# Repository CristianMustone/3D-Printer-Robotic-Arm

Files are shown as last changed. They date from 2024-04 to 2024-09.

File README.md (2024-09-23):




# Robotic Arm 3D Printer #

A robotic arm with 3 degrees of freedom will be made, one prismatic and two rotating, with a SCARA – PRR type distribution.
The stepper motors corresponding to each degree of freedom will be controlled through an Arduino Uno together with L298N controllers.
A connection function via WIFI will be added with the integration of an ESP32 Cam, which communicates with the Arduino Uno, with which the G code file (.GCODE) of the part to be printed can be sent, and it will begin automatically . Communication between the computer where the G code is located and the ESP32 of the printer will be carried out through the website. With further development, it could be controlled over long distances through web pages, for example.
In a future application, the printing base could be replaced with a ribbon that withstands the extrusion temperature in order to have a level of serial production higher than most of the machines available on the market.

<table>
  <tr>
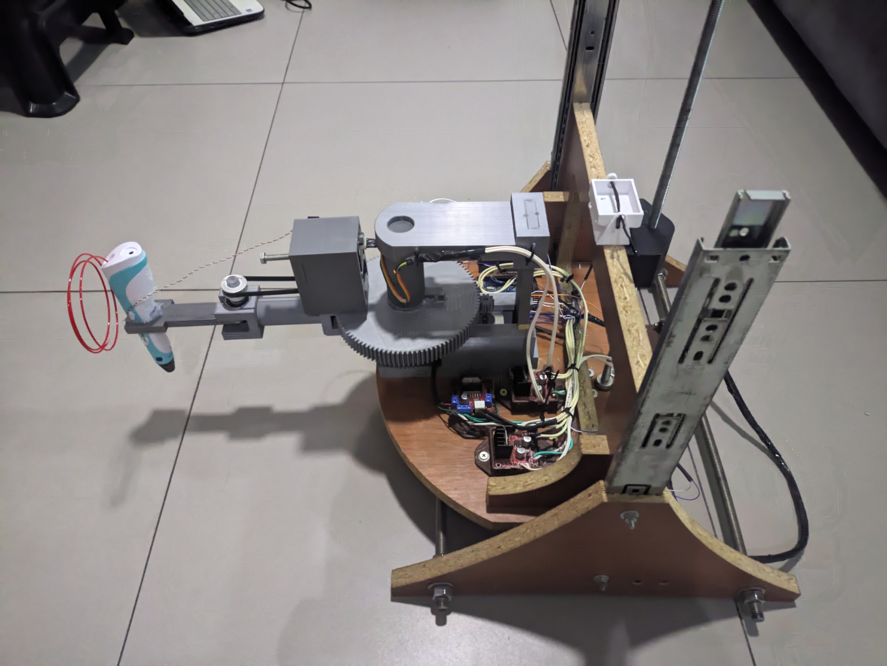
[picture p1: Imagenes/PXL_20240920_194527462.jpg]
Imagen 1
    <td></td>
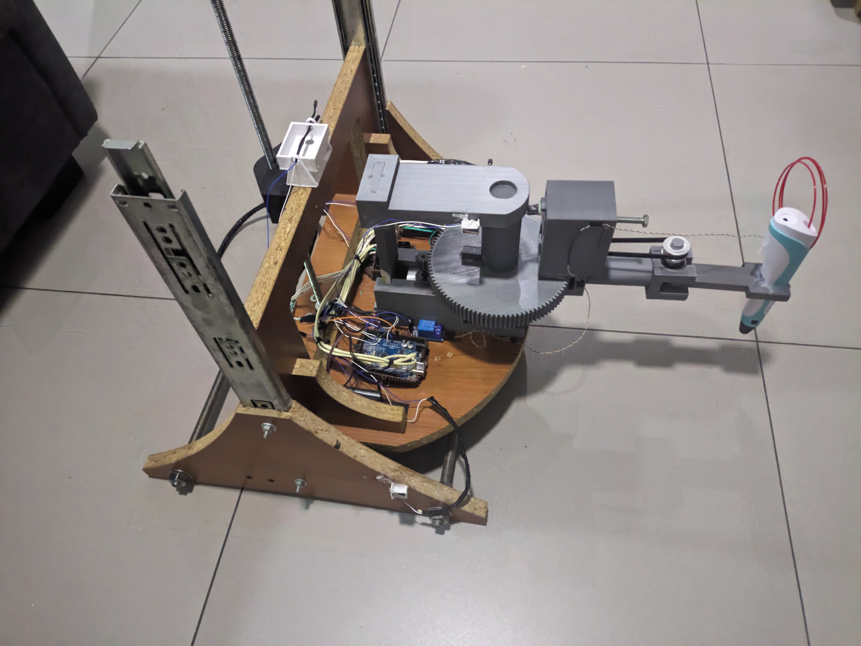
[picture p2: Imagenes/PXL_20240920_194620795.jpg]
Imagen 3
    <td></td>
  </tr>
  <tr>
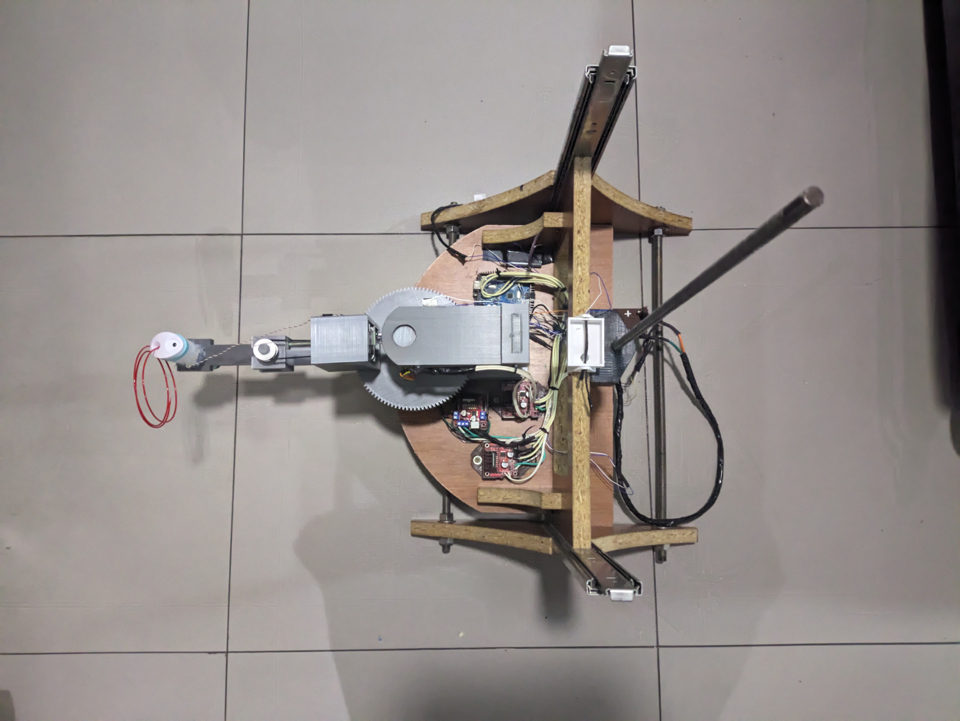
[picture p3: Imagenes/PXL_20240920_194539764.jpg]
Imagen 3
    <td></td>
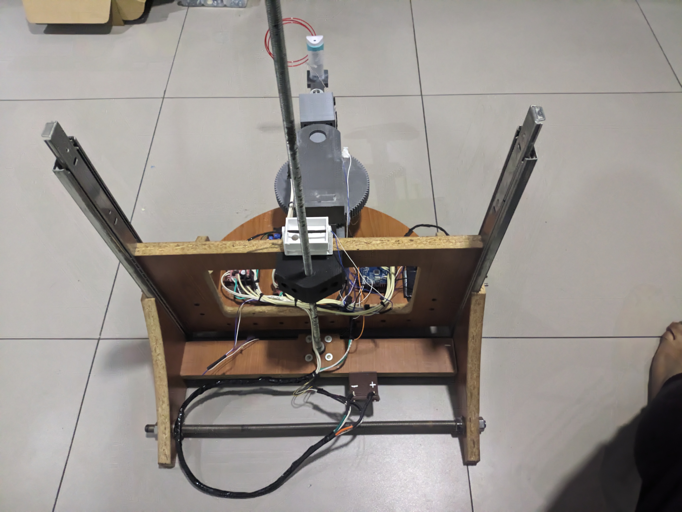
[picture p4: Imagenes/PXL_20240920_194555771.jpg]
Imagen 4
    <td></td>
  </tr>
  <tr>
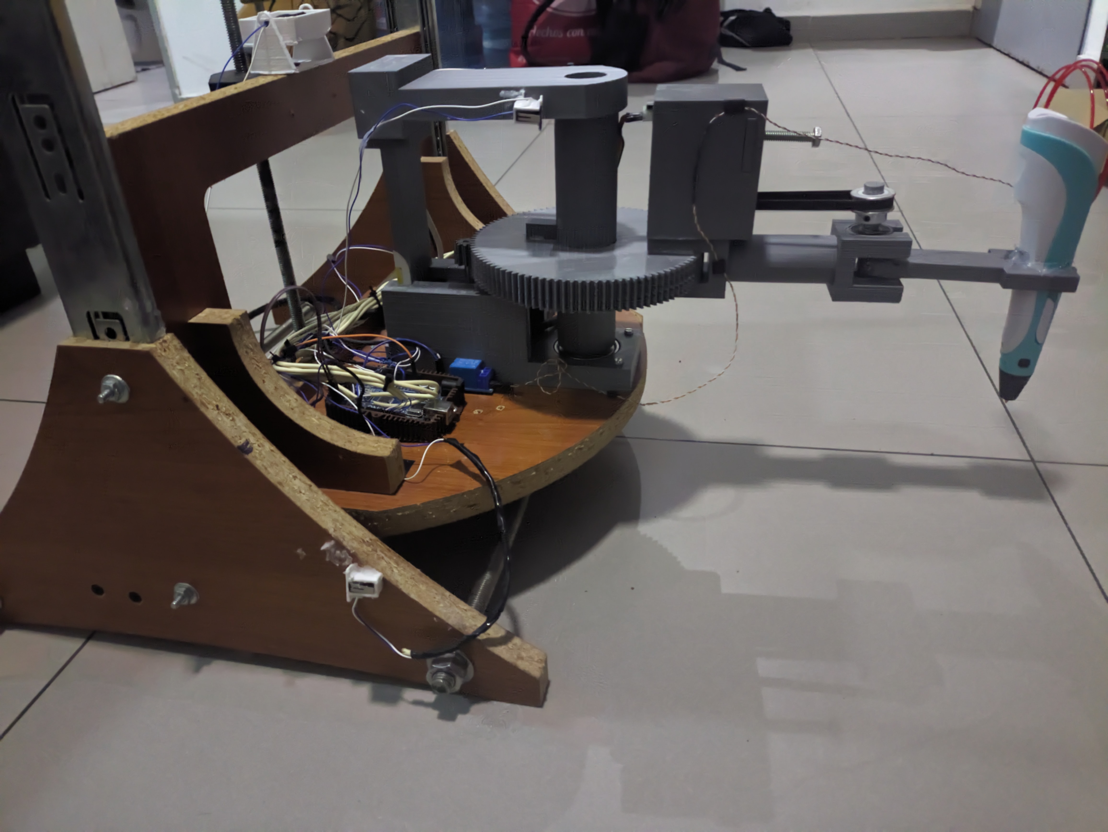
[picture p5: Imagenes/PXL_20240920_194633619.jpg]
Imagen 3
    <td></td>
    <td>Imagen 4</td>
  </tr>
</table>

## Goals

This project seeks to design a 3D printing system different from the most common models on the market, such as the 3-axis printer or those with an infinite axis. In addition, it will have greater printing capacity in terms of the size of the prints it can make, since being an instrument widely used today, there is a need to print larger pieces at once.
It also seeks to improve the human-printer relationship through online communication, either to show the progress of the printing or to attach a new job without having to connect it to a PC or through a compatible memory card.
Another objective is to be able to build a printer that entails lower manufacturing costs in order to compete with other printers on the market that have a higher price for equal or inferior features.

## Summary

A robotic arm with 3 degrees of freedom will be developed, with a configuration of 1 prismatic axis that will be used for the vertical movement of the extruder, and 2 rotary axes in SCARA format.
The advantage of this configuration is that it gives us a 180° printing area, a reach of 41 cm (base can be modified according to characteristics) and a height of approximately 30 cm. In total it would be a printing area of [Printing area calculation].
The parts to be used will be made of PLA, since they were designed and printed in 3D, wood, for the supports and components that require greater resistance, and finally the electronic components are integrated.
The operation is based on sending the file with a .gcode extension that is obtained from any laminator on the market (such as Cura) through a web page, and which can be printed automatically without requiring physical access to the machine. It will also have a camera that can be accessed from the same website to see the progress of the 3D printing made by the arm.

## Technical specifications

- The robotic arm must have an adequate range of motion to cover the minimum print area of 300x300x300.
- The robotic arm must be equipped with an extrusion tool that can print both PLA and ABS and the head itself must be able to be easily exchanged
- It must be operated through a Wi-Fi network from a web page with a user-friendly interface which is capable of loading a direct parameterized file to print and be able to initialize the operation as well as be able to see the process in real time through the application.
- The wireless connection must be stable and secure to guarantee fluid communication between the printer and the application.
- The structure of the robotic arm must be robust and resistant to ensure stable and safe operation.
- The manufacturing cost of the robotic arm should be as low as possible without compromising the quality and efficiency of the system.
- The robotic arm should be easy to disassemble and maintain to facilitate repair and replacement of parts in case of failure.Principle of form
- The structure must be stable and of simple design that guarantees possible future sizing applications.

# Materials

| Material | Quantity |
|---|:---:|
| L298N | x3 |
| Stepper NEMA 17 | x3|
| Cables |
| Arduino Uno | x1|
| ESP32 | x1|
| ESP32 CAM | x1|
| Wood |
| Power Supply 12v / 5v |
| Pencil 3D Printer | x1|
| Threaded Rod | x1|

## Selection criteria for each material

### ARDUINO UNO
The Arduino was selected as the motherboard for the movement of the motors due to the large number of libraries that can be found on the market for this type of boards, in addition to the ease they provide when programming the movement sequence.
The ESP32 or the ESP32 CAM was not used directly since, although the libraries can be adapted to this type of boards, the use of Wi-Fi required multiple use of pins to connect to the Internet and also move the motors, which generated unwanted signals that produced unwanted movements in the motors or their non-functioning at all.

### ESP32
This board was selected since it offers us the possibility of connecting to the Internet through an integrated Wi-Fi connection without the need to incorporate integrated devices.

### ESP32 CAM
This board was selected due to a similar criterion as the ESP32, it provides us with an integrated camera capable of transmitting video via Wi-Fi without a physical connection to the equipment through an IP address of the device.

## Design Specifications
It will be constructed constructively from parts made in 3D printing and wood, mainly ignoring the electronic and transmission components, the design will be based on figure 1 with modifications according to the needs.
The 3D printed parts were designed by ourselves. An approach was taken that with the smallest amount of material possible a part could be generated with the same functionality and that would withstand the conditions to which it was subjected. A 20% infill configuration was used and the material to be used was PLA.

# Software to Use

The following components will be programmed using C language:
ESP32: This will be used to communicate the webpage where the code is uploaded with the ARDUINO UNO.
ARDUINO UNO: This development board will be used to transform the code received from the user into one that the robot can use, and also to command the motors to be used.
ESP32 CAM: This will be used from the webpage for remote monitoring of the printing process.
A combination of HTML and CSS will also be used for the webpage design.

The steps for the complete functioning of the project are as follows:

1. File Upload: The file to be printed is uploaded to the webpage. This performs an HTTP POST of the file's content to a Google Sheets document. 
2. Handling from Google Sheets: The Google Sheets document is configured to, upon receiving an HTTP POST, capture all the sent content and place it line by line in the first column of its only sheet. Similarly, when it receives an HTTP GET, it sends all the information from the first column as a single string, where each line is separated by a comma.
3. Retrieval by the ESP32: The ESP32 is programmed to perform an HTTP GET to the Google Sheets document. Upon obtaining the string with the uploaded code, it executes a function to remove all unnecessary lines for motor operation, such as pre-configurations, extruder management, etc.
4. Sending to ARDUINO UNO: Once all the information is filtered, the ESP32 sends the newly generated string via the serial port (TX and RX) to the ARDUINO UNO.
5.The ARDUINO UNO performs further processing of the string where, for each command line of the code, it obtains the destination positions for both X and Y.
6. Once the positions are obtained, it calls a function that calculates the number of steps each motor needs to take according to our movement system.
7. With the number of steps calculated, we use another function that commands the motors to move the calculated number of steps, synchronously for the X and Y axes to maintain a stepped movement along the displacement vector.
8. Use of the ESP32 CAM: The ESP32 CAM code is set to work inversely to the ESP32. It generates an IP for the integrated camera and performs an HTTP POST with its IP address to another Google Sheets document.
9. When the webpage requests to view the printing progress, it first performs an HTTP GET to the Google Sheets document where the IP address of the ESP32 CAM is stored, then it directs to this address to display the video being recorded by the ESP32 CAM showing the printing progress.

## Explanation of how the code works
### Code explanation for the Arduino Uno
We are going to stop specifically at this point in order to detail the method of operation of the transformation of the Cartesian positions obtained to the number of steps that each motor must move along with the speed at which they must do so.
``` sh
while (Serial.available() > 0 && MensajeRecibido==0) {
    receivedMessage = Serial.readStringUntil('\r');
    Serial.println("Mensaje Recibido");
    Serial.println(receivedMessage);
    //miCadena.indexOf(subCadena)
    if ( receivedMessage.indexOf(",") != -1 && receivedMessage.indexOf(";") != -1){
      MensajeRecibido=1;
    }
```
This code fragment is used to enable reading the Serial port of the arduino while waiting for the message sent by the ESP32 with the string that has the lines of code to be executed by the robot.

``` sh
void MatrizMovimientos(char texto[]){
  for (int i = 0; i < strlen(texto); i++) {
    if (texto[i] == ';') {
      filas++;
    }
  }
  char *token = strtok(texto, ",;");
  for (int i = 0; i < filas; i++) {
    for (int j = 0; j < columnas; j++) {
      Movimientos[i][j] = atoi(token);
      // Serial.print("Valor Leido: ");
      // Serial.println(Movimientos[i][j]);
      token = strtok(NULL, ",;");
    }
  }
```
Next, the first function to use is to generate the Movement Matrix, that is, a list is created with the final positions of each axis for each line of code received. This generates a list with 3 values in each element, these values being the final positions of (X, Y, Z) .

``` sh
void moverRobotSCARA(float x, float y) {
  // Función para mover el robot SCARA a una posición específica
  int cuadrante = 0; 
  x=abs(x);
  y=abs(y);

  float d = sqrt(x * x + y * y);
  float phi = atan2(y, x);
  // Calcular los ángulos de las articulaciones mediante cinemática inversa
  float theta2 = acos((d * d - L1 * L1 - L2 * L2) / (2 * L1 * L2));
  float theta1 = phi - atan2(L2 * sin(theta2), L1 + L2 * cos(theta2));
  // Convertir los ángulos a pasos para los motores paso a paso
  float avanzar1 = ((theta1 - ultimo_step1) * 360)/(2 * PI);
  float avanzar2 = ((theta2 - ultimo_step2) * 360)/(2 * PI);

  int steps1 = avanzar1 / avance_motor;
  int steps2 = avanzar2 / avance_motor;

  MoverBrazo(steps1, steps2);

  ultimo_step1 = steps1;
  ultimo_step2 = steps2;
}
```

In the case of the moveRobotSCARA function, it is the one that transforms the final positions into the number of steps for each motor, only in the case of motors 1 and 2 (that is why it has 2 input values), representatives of the X and Y axes. , since, as they were defined as rotary type axes, a transformation from Cartesian coordinates to polar coordinates is necessary for their use.
Due to the configuration of the axes, it was decided to use the geometric method to calculate the angles to rotate in each motor in order to make the calculation simpler. We can observe the development of this method in the first lines of the function; converting them to mathematical language they would be:

$$ d = x2+ y2 $$

Calculates the distance from the origin to the end point where the extruder is located

$$phi = arc tangent (y,x)$$

To calculate the angle at which the end point is with respect to the horizontal axis

$$theta2 = arc cosine((d * d - L1 * L1 - L2 * L2) / (2 * L1 * L2))$$

L1 and L2 represent the lengths of arms 1 and 2 respectively.
This formula is used to calculate the angle between arm 2 and the continuation of the center line of arm 1.

$$theta1 = phi - arctangent(L2 * sine(theta2), L1 + L2 * cosine(theta2))$$

Finally, the angle of arm 1 with respect to the horizontal axis is calculated.

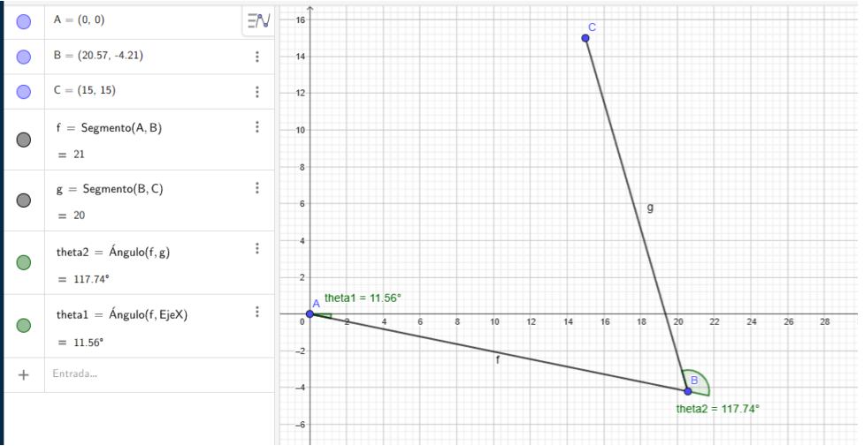
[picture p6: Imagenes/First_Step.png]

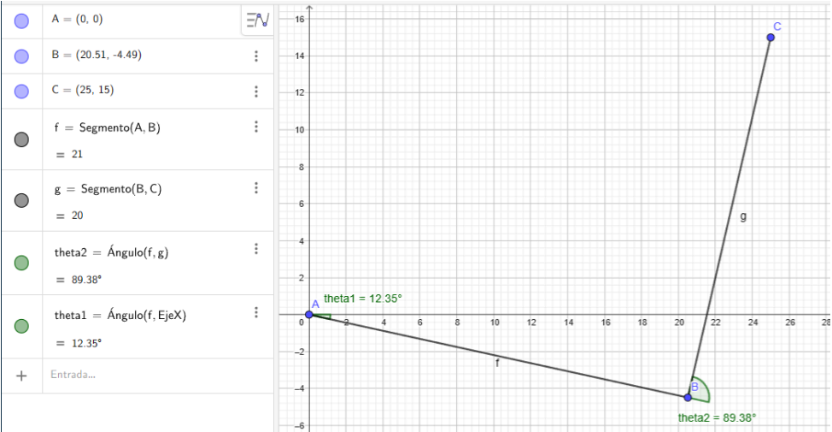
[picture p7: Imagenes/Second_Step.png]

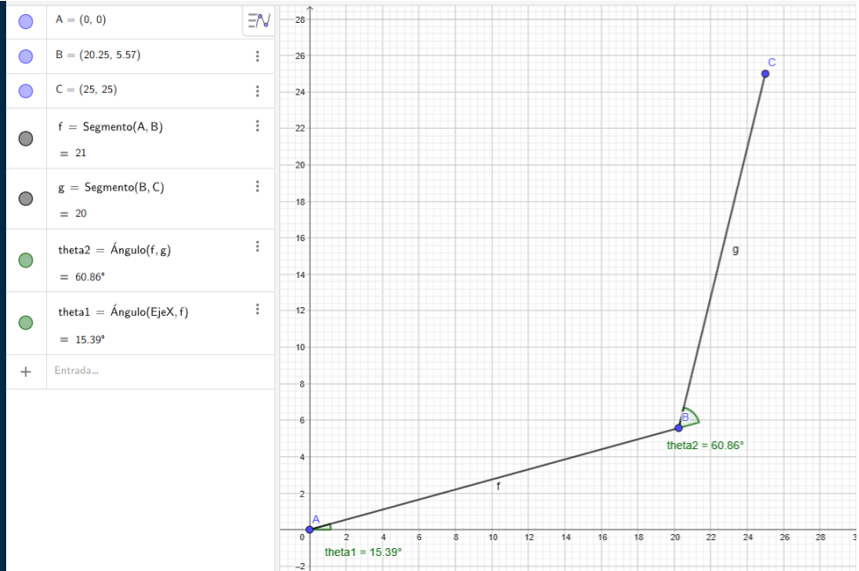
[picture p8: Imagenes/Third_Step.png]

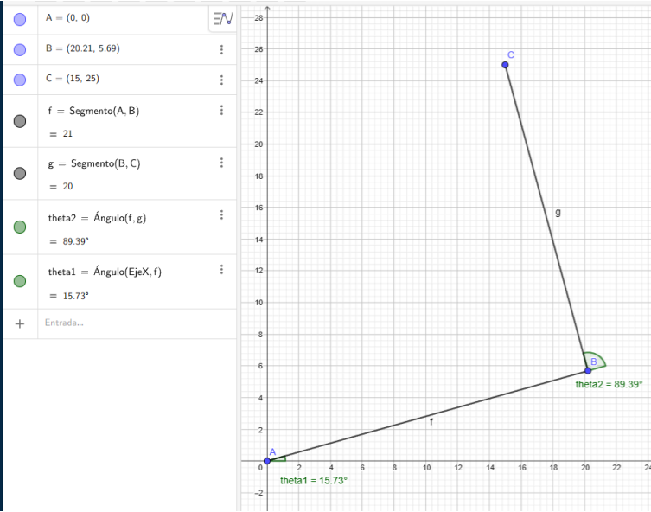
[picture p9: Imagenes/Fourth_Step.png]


Recreating the movement of the robot, the previous sequence of steps would look like:

video

With the sequence of end points (15,15); (25,15); (25,25); (15.25) the angles of theta1 and theta2 should be as follows:

```sh
  float avanzar1 = ((theta1 - ultimo_step1) * 360)/(2 * PI);
  float avanzar2 = ((theta2 - ultimo_step2) * 360)/(2 * PI);

  int steps1 = avanzar1 / avance_motor;
  int steps2 = avanzar2 / avance_moto
```
Next, the angles that each motor must advance (or retreat) are calculated. This is calculated by converting the calculated angles to geometric degrees, since they are initially found in non-representative values, that is, values that cannot be used as geometric degrees.
The angle at which the motor is currently located will also be subtracted, reflected in the variables ultimo_step1 and ultimo_step2, which, after each movement, will be updated. For example, if motor counterpart to advance1 but stops motor 2)
Finally, the number of degrees to move in each motor is divided by the degrees per step of the motor (in this case it would be 1.8 degrees per step, which is stored in the variable advance_motor), obtaining the number of steps to be performed to advance that number of geometric degrees.
```sh
MoverBrazo(steps1, steps2);
```
Once the entire series of calculations is finished, the MoveArm function is called, which is responsible for coordinating the movements of motors 1 and 2 so that they reach their destination at the same time, generating a straight line as a trajectory.
```sh
void MoverBrazo(int pasosX, int pasosY){
  int timeX = 0;
  int timeY = 0;
  int timetotal = 0;
  if (pasosX!=0 && pasosY!=0){
    float relacion = abs(pasosX)/abs(pasosY);
    stepDelayX = stepDelayX * pow(relacion,(-1));
  	timetotal = abs(pasosX) * stepDelayX;
  } else if (pasosY==0 && pasosX!=0){
  	timetotal = abs(pasosX)* stepDelayX;
  } else {
    timetotal = abs(pasosY)* stepDelayY;
  }

  for(int i=0;i<=timetotal;i++){
    if (i-timeX >= stepDelayX){
      if (pasosX>0){
        motorX.step(1);
      } else if (pasosX<0){
        motorX.step(-1);
      }
      timeX = i;
    }
    if (i-timeY >= stepDelayY){
      if (pasosY>0){
        motorY.step(1);
      } else if (pasosY<0){
          motorY.step(-1);
        }
      timeY = i;
  	}	
    delay(1);
  }
}
```
For motor hands to reach the destination point at the same time, regardless of the number of steps each one must take, there were several possibilities, such as using the Arduino milis library, but in this case it was decided to make a function with a Similar operation but with very short delay.
The operation of the MoverRoborSCARA function calculates the ratio of steps that motor 1 and 2 must take, once obtained, it affects the delay or internal speed of the motor with fewer steps by that factor, and it is obtained that both motors take the same even if they take a different number of steps. It should be noted that both motors already have a minimum speed for movement, so the factor is always additive.
Once the time that both motors will take to complete their corresponding steps has been calculated, a for loop is created that iterates for each millisecond of the total calculated, and at the end a delay of 1 millisecond is placed, this will cause each cycle of the loop to be executed every 1 millisecond. This allows us to see if the delay of each motor, that is, the number of milliseconds it takes to take each step, corresponds to the cycle number that is being executed, the motor moves one step. This affects both engines at the same time.
When you have to move a step regardless of the motor, a conditional is added to know if you have to move clockwise or counterclockwise, it could also be said, if you have to move one step or less one step.
As you can see, the operation of the Arduino milis library is very similar but with the addition of greater control over the total duration time.

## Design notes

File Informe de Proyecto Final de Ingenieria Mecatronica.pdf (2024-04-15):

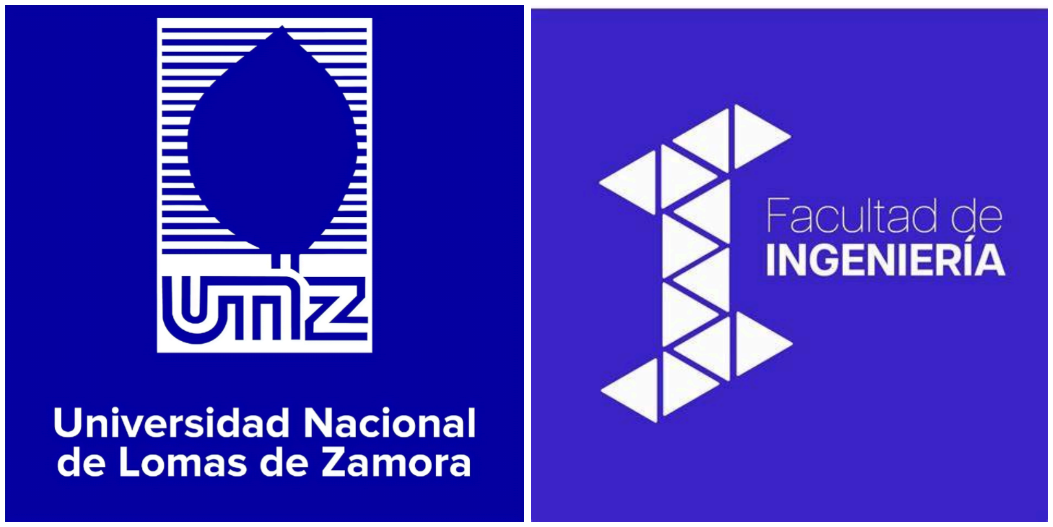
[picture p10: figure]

# INFORME

Alumnos:
Cristian Nahuel Castañares DNI: 42339695
MAIL: crismust99@gmail.com

Materia:
Proyecto Final de Ingeniería Mecatrónica

Carrera:
Ingeniería Mecatrónica

Facultad de Ingeniería - Universidad Nacional de Lomas de Zamora | 1

# Observaciones

Informe de proyecto final de Ingeniería Mecatrónica

Facultad de Ingeniería - Universidad Nacional de Lomas de Zamora | 2

# Armado de brazo robótico para imprimir en3D utilizando plástico fundido

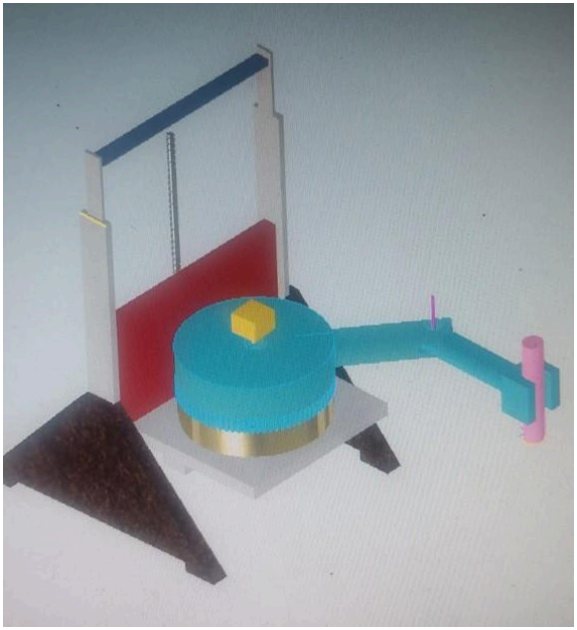
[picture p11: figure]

Facultad de Ingeniería - Universidad Nacional de Lomas de Zamora | 3

# Índice

Facultad de Ingeniería - Universidad Nacional de Lomas de Zamora | 4

# 1.Presentación

## 1.1 Introducción

Se realizará un brazo robótico de 3 grados de libertad, uno prismático y dos rotativos, con una distribución tipo SCARA – PRR.
Se controlarán los motores paso a paso correspondientes a cada grado de libertad, a través de un Arduino Uno junto con controladores Pololu A4988.
Se agregará una función de conexión a través de WIFI con la integración de un ESP32 Cam, que se intercomunica con el Arduino Uno, con el cual se podrá enviar el archivo en código G (.GCODE) de la pieza a imprimir, y comenzará automáticamente. La comunicación entre la computadora donde se encuentra el código G y el ESP32 de la impresora, se realizará a través de la pagina web. Con un desarrollo mayor, se podría controlar a distancias grandes a través de páginas web, por ejemplo.
En una futura aplicación se podría reemplazar la base de impresión por una cinta que soporte la temperatura de extrusión a fin de poder contar con un nivel de producción en serie superior a la mayoría de las máquinas disponibles en el mercado.

Facultad de Ingeniería - Universidad Nacional de Lomas de Zamora | 5

## 1.2 Objetivos

- En este proyecto se busca diseñar un sistema de impresión 3D diferente a los modelos más comunes del mercado, como la impresora de 3 ejes o las de un eje infinito. Además, tendrá mayor capacidad de impresión en cuanto al tamaño de las impresiones que pueda realizar, ya que al ser un instrumento bastante utilizado en la actualidad, nace una necesidad de imprimir piezas más grandes de una sola vez.
- También se busca mejorar la relación humano – impresora a través de una comunicación online, ya sea para mostrar el avance de la impresión como también adjuntarle un nuevo trabajo sin necesidad de conectarla a una PC o a través de una tarjeta de memoria compatible.
- Otro de los objetivos es poder construir una impresora que conlleve un menor gasto de fabricación para así competir con demás impresoras en el mercado que posean un precio mayor por características iguales o inferiores.

Facultad de Ingeniería - Universidad Nacional de Lomas de Zamora | 6

## 1.3 Alcance

- Para el alcance de este proyecto, se tendrán en cuentas las siguientes modificaciones al proyecto inicialmente descripto:
- Se reemplazará el extrusor normalmente utilizado en impresoras 3D por un lápiz que cumple la misma funcionalidad pero con la ventaja de ser mucho más sencillo de utilizar.
- No se tendrá en cuenta el eje infinito para producción en serie, y se trabajará solamente con el área de impresión física del robot.
- La comunicación entre la computadora y la impresora será a través de wifi en la cual ambos dispositivos deberán estar conectado a la misma red.

Facultad de Ingeniería - Universidad Nacional de Lomas de Zamora | 7

## 1.4 Resumen

Se elaborará un brazo robótico de 3 grados de libertad, con una configuración de 1 eje prismático que se utilizara para el movimiento vertical de la extrusora, y 2 ejes rotativos en formato SCARA.
La ventaja de esta configuración es que nos da un área de impresión de 180°, un alcance de 41 cm (de base pudiendo modificar según características) y una altura de 30 cm aproximadamente. En total seria una area de impresion de [Calculo del area de impresion]. Las piezas a utilizar serán de PLA, ya que se diseñaron e imprimieron en 3D, madera, para los soportes y componentes que requieran una resistencia mayor, y por último se integran los componentes electrónicos.
El funcionamiento se basa en el envío del archivo con extensión .gcode que se obtiene en cualquier laminador del mercado (como por ejemplo Cura) a través de una página web, y que pueda imprimirse automáticamente sin necesitar de tener acceso físico a la máquina. También contará con una cámara a la que se podrá acceder desde la misma página web para ir viendo el avance de la impresión 3D realizada por el brazo.

Facultad de Ingeniería - Universidad Nacional de Lomas de Zamora | 8

# 2. Ingeniería de la solución

## 2.1 Especificaciones técnicas:

- El brazo robótico debe tener un rango de movimiento adecuado para cubrir el área de impresión mínima de 300x300x300.
- El brazo robótico debe estar equipado con una herramienta de extrusión que pueda imprimir tanto pla como abs y el mismo cabezal debe ser capaz de intercambiarse fácilmente
- Se debe operar mediante una red wifi a partir de una página web con una interfaz amigable con el usuario la cual sea capaz de cargar un archivo parametrizado directo para imprimir y poder inicializar la operación así como poder ver mediante el aplicativo el proceso en tiempo real
- La conexión inalámbrica debe ser estable y segura para garantizar una comunicación fluida entre la impresora y el aplicativo.
- La estructura del brazo robótico debe ser robusta y resistente para garantizar una operación estable y segura.
- El costo de fabricación del brazo robótico debe ser lo más bajo posible sin comprometer la calidad y la eficiencia del sistema.
- El brazo robótico debe ser fácil de desmontar y mantener para facilitar la reparación y el reemplazo de piezas en caso de fallos.Principio del formulario
- La estructura debe ser estable y de diseño simple que garantice posibles aplicaciones de dimensionamiento a futuro.

## 2.2 Detalle de pines a utilizar

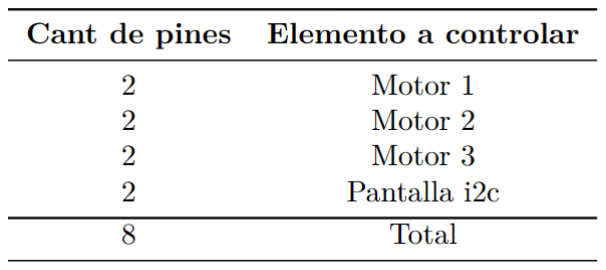
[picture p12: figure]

Facultad de Ingeniería - Universidad Nacional de Lomas de Zamora | 9

## 2.3 Materiales a utilizar

### 2.3.1 Presupuesto

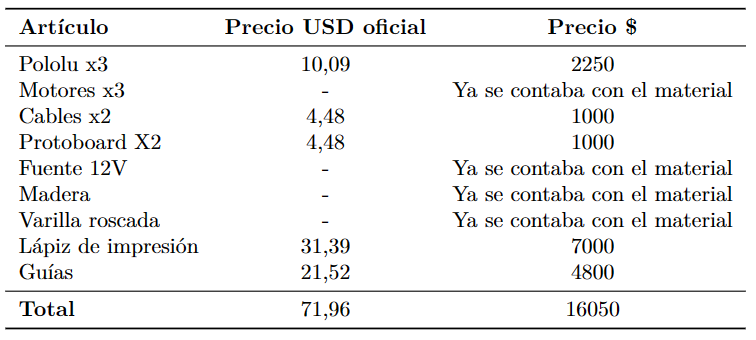
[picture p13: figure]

### 2.3.2 Criterio de selección de cada material

ARDUINO UNO
Se seleccionó el Arduino como placa base para el movimiento de los motores debido a la gran cantidad de librerías que se pueden encontrar en el mercado para este tipo de placas, además de la facilidad que otorgan a la hora de programar la secuencia de movimiento.
No se utilizó directamente el ESP32 o el ESP32 CAM ya que, si bien puede adaptarse las librerías a este tipo de placas, el uso del wifi requería multiuso de pines para conectarse a internet y además mover los motores, lo cual generaba señales indeseadas que producían movimientos no deseados en los motores o directamente su no funcionamiento.

ESP32
Se seleccionó esta placa ya que nos ofrece la posibilidad de conectarnos a internet a través de una conexión wifi integrada sin necesidad de incorporar integrados.

ESP32 CAM
Esta placa se seleccionó debido a un criterio similar al del ESP32, nos brinda una cámara integrada capaz de transmitir video a través de wifi sin conexión física con el equipo a través de una dirección IP del dispositivo.

## 2.4 Especificaciones de Diseño

El mismo será construido constructivamente a partir de piezas elaboradas en impresión 3D y madera principalmente obviando los componentes electrónicos y de transmisión, el diseño será basado en la figura 1 con las modificaciones acordes a las necesidades.
Las piezas impresas en 3D fueron diseñadas por nosotros mismos. Se tuvo un enfoque de que con la menor cantidad de material posible se pueda generar una pieza con la misma

Facultad de Ingeniería - Universidad Nacional de Lomas de Zamora | 10

funcionalidad y que soportara las condiciones a la que se estaba sometido. Se utilizó una configuración de relleno del 20% y el material a utilizar fue PLA.
Para las piezas compuestas por madera, se utilizó una cortadora láser y tablas de [material].

[piezas impresas]

## 2.5 Software a utilizar

Se usará lenguaje C para programar los siguientes componentes:
- ESP32: El cual se utilizará para comunicar la página web donde se depositara el código con el ARDUINO UNO.
- ARDUINO UNO: Se utilizará esta placa de desarrollo para la transformación del código recibido por el usuario a uno que el robot pueda utilizar, y además para el comando de los motores a utilizar.
- ESP32 CAM: En este caso se utilizará desde la página web para el seguimiento de la impresión a distancia.
También se utilizará una combinación de HTML y CSS para el diseño de la página web.

Los pasos a seguir para el funcionamiento completo del proyecto son:

### 1. Subida del archivo: Se sube el archivo que se quiere imprimir a la página web. Esta

realiza un HTTP POST del contenido del archivo a un archivo de Google sheets

### 2. Manejo desde Google Sheets: El archivo de Google Sheets está configurado para

que cuando recibe un HTTP POST, obtenga todo el contenido que se le ha enviado y lo coloque por línea en la primera columna de la única hoja que se encuentra en el documento. De la misma forma, cuando recibe un HTTP GET, envía toda la información de la primera columna en un solo string, en el cual cada línea está separada por una coma.

### 3. Obtención desde el ESP32: El ESP32 está programado para realizar un HTTP

GET al archivo del Google Sheets. Cuando obtiene el string con el código subido, ejecuta una función que elimina todas las líneas innecesarias para el funcionamiento de los motores, ya sean pre configuraciones, manejo del extrusor, etc.

### 4. Envío al ARDUINO UNO: Una vez filtrada toda la información, el ESP32 envía el

nuevo string generado a través del puerto serie (TX y RX) hacia el ARDUINO UNO.
a. Este hace un segundo manejo del string en donde, por cada línea de comando del código, obtiene las posiciones de destino tanto de X como Y.
b. Una vez obtenidas las posiciones, manda a llamar a la función que calcula la cantidad de pasos que debe realizar cada motor según nuestro sistema de movimiento.
c. Cuando calcula la cantidad de pasos manda a llamar a otra función que es la que comanda a los motores, diciendo que se muevan la cantidad de pasos calculados, junto con una configuración para manejar los tiempos de movimiento de cada motor.

### 5. Uso del ES32 CAM: El código del ESP32 CAM está seteado para funcionar a la

inversa del ESP32, este genera una IP para la cámara que está integrada, y realiza un HTTP POST con su dirección IP a otro archivo de Google Sheets.
Cuando la página web solicita ver el avance de la impresión, realiza primero un HTTP GET al archivo de Google Sheets donde esta la direccion IP de la cámara del

Facultad de Ingeniería - Universidad Nacional de Lomas de Zamora | 11

ESP32 CAM, para dirigirse a esta y mostrar el video que está filmando el ESP32 CAM con el avance de la impresión.

### 2.5.1 Código del ESP32

Para este caso, a fin de un mejor control, orden y revisión del código, se decidió separarlo en 2 módulos complementarios. En uno se definen las funciones que se van a utilizar mientras en el otro se utilizan y arma el código general.
El módulo general quedaría de la siguiente forma:

#include <HardwareSerial.h>

#include <WiFi.h>

#include <HTTPClient.h>

#include <string.h>

#define esp32TX 1 // Puedes ajustar los pines según tu configuración #define esp32RX 3

#define WIFI_SSID "PCwifi"

#define WIFI_PASSWORD "ingmustone"

String GOOGLE_SCRIPT_ID =
"AKfycbxiWrbWpRyaDDQQgARydaQq3UQNIaPEfO08l73xLwA0IrmX1_svnYCXUWWWk37 KXSlUqg";

#define MAX_COMMAND_LENGTH 255

int SendMessage=0;
char gcode_string[1024]; // Tamaño suficiente para almacenar las líneas del archivo int FileOk = 1;
const char* payloadCopy;
int Filas = 0;
int Movimientos[50][3]; // cantidad de filas que va contener se estima en 50 por ahora char Mensaje[1024]="";

void setup() {
Serial.begin(115200);
Serial2.begin(2400, SERIAL_8N1, esp32RX, esp32TX); // Inicializa Serial2 con pines personalizados

String payload;

WiFi.begin(WIFI_SSID, WIFI_PASSWORD);

while (WiFi.status() != WL_CONNECTED) { delay(500);

Facultad de Ingeniería - Universidad Nacional de Lomas de Zamora | 12

Serial.println("Conectando");
}

HTTPClient http;
String url="https://script.google.com/macros/s/"+GOOGLE_SCRIPT_ID+"/exec?read"; http.begin(url.c_str()); //Specify the URL and certificate http.setFollowRedirects(HTTPC_STRICT_FOLLOW_REDIRECTS);
int httpCode = http.GET();
if (httpCode > 0) { //Check for the returning code
payload = http.getString();
payloadCopy=payload.c_str(); Serial.println("HTTP ok");
}
http.end();

}

void loop() {
if (SendMessage==0){
strcpy(gcode_string, payloadCopy); Serial.println("Armando Matriz de Movimientos"); MatrizDeMovimientos(gcode_string); Serial.println("Matriz Armada");

for (int Fila=0; Fila<Filas; Fila++){
char numero[20];
sprintf(numero, "%d", Movimientos[Fila][0]); strcat(Mensaje, numero);
strcat(Mensaje,",");
sprintf(numero, "%d", Movimientos[Fila][1]); strcat(Mensaje, numero);
strcat(Mensaje,",");
sprintf(numero, "%d", Movimientos[Fila][2]); strcat(Mensaje, numero);
strcat(Mensaje,";");
}

Serial2.println(Mensaje);
SendMessage=1;
}
}

Mientras que el módulo de las funciones quedaría de la siguiente forma:

bool TryCatch (char Letra, const char* line){
char* Pos=0;
//PosZ=*(strchr(line,'Z'));

Facultad de Ingeniería - Universidad Nacional de Lomas de Zamora | 13

bool success = true;
Pos=strchr(line,Letra);
return success;
}

void extractSubstring(const char* input, char* output, size_t startIndex, size_t length) { size_t inputLength = strlen(input);
if (startIndex >= inputLength) {
// Error: startIndex está fuera de los límites de la cadena de entrada
return;
}
size_t endIndex = startIndex + length;
if (endIndex > inputLength) {
// Ajustar endIndex si excede la longitud de la cadena de entrada endIndex = inputLength;
}

strncpy(output, input + startIndex, endIndex - startIndex); output[endIndex - startIndex] = '\0';
}

void MatrizDeMovimientos(char* gcode_string){
int comandoG = 0;
char* line;
line = strtok(gcode_string, ",");
while (line != NULL) {
if (line[0] == 'G') {
comandoG = 1;

char newX[20]="0";
char newY[20]="0";
char newZ[20]="0";
char* PosX = 0;
char* PosY = 0;
char* PosZ = 0;
char* PosE = 0;
bool Fx, Fy, Fz, Fe = true; size_t Px,Py,Pe,Pz=0;

switch (line[1]){
case '0':
/*X e Y Siempre
E nunca
Z quizas*/
//------------------------------------- Extrayendo Z si la hay ----------------------------if (TryCatch('Z',line)){
PosZ=strchr(line,'Z');
Pz = PosZ - line;

Facultad de Ingeniería - Universidad Nacional de Lomas de Zamora | 14

size_t lengthZ = strlen(line) - Pz;
extractSubstring(line, newZ, Pz + 1, lengthZ);
Fz = true;
} else {
Fz = false;
}
//------------------------------------- Extrayendo X e Y ----------------------------//obtengo la posicion de X e Y

PosX=strchr(line,'X');
Px= PosX - line;
Fx = true;

PosY=strchr(line,'Y');
Py = PosY - line;
Fy = true;

if (Fx && Fy){
size_t lengthX = Py - Px - 1; extractSubstring(line, newX, Px + 1, lengthX); }
if (Fy && Fz){
size_t lengthY = Pz - Py - 1; extractSubstring(line, newY, Py + 1, lengthY); } else {
size_t lengthY = strlen(line) - Py + 1; extractSubstring(line, newY, Py + 1, lengthY); }

Movimientos[Filas][0] = atof(newX); Movimientos[Filas][1] = atof(newY); Movimientos[Filas][2] = atof(newZ);

break;

case '1':
/*X e Y quizas
E siempre
Z nunca*/
//------------------- Revisando si hay X e Y ---------------------------------if (TryCatch('X',line)){
PosX=strchr(line,'X');
Px= PosX - line;
Fx=true;
} else {
Fx = false;
}

Facultad de Ingeniería - Universidad Nacional de Lomas de Zamora | 15

if (TryCatch('Y',line)){
PosY=strchr(line,'Y');
Py = PosY - line;
Fy=true;
} else {
Fy = false;
}
if (TryCatch('E',line)){
PosE=strchr(line,'E');
Pe = PosE - line;
Fe=true;
} else {
Fe = false;
}
if (Fx && Fy){
size_t lengthX = Py - Px - 1; extractSubstring(line, newX, Px + 1, lengthX); }
if (Fy && Fe){
size_t lengthY = Pe - Py - 1; extractSubstring(line, newY, Py + 1, lengthY); }

Movimientos[Filas][0] = atof(newX); Movimientos[Filas][1] = atof(newY); Movimientos[Filas][2] = 0;

break;
default:
break;
}
Filas++;
}
line = strtok(NULL, ",");
}
}

### 2.5.2 Código para el Arduino Uno

En este caso también se decidió tener dos módulos similares al caso anterior. De los cuales el código general quedaría:

#include <Stepper.h>

#include <math.h>

#include <stdlib.h>

#include <string.h>

Facultad de Ingeniería - Universidad Nacional de Lomas de Zamora | 16

String receivedMessage = "";
int MensajeRecibido = 1;

// Define el número de pasos por vuelta del motor
const int stepsPerRevolutionZ = 200; //suponiendo que es 1mm por vuelta const int stepsPerRevolutionX = 1600; //suponiendo que la relacion es 80:1 const int stepsPerRevolutionY = 200; //la relacion es 1:1

// Define los pines de control para el driver L298N
const int motor1Pins[] = {2,3, 4, 5}; // IN1, IN2, IN3, IN4
const int motor2Pins[] = {6, 7, 8, 9}; // IN1, IN2, IN3, IN4
const int motor3Pins[] = {10, 11, 12, 13}; // IN1, IN2, IN3, IN4

int filas = 0, columnas = 3;
int Movimientos[50][3]; // cantidad de filas que va contener se estima en 50 por ahora

#define L1 21.0 // Longitud del primer eslabón en unidades de longitud

#define L2 20.0 // Longitud del segundo eslabón en unidades de longitud

#define avance_motor 1.8

// Crea objetos Stepper para cada motor
Stepper motorX(stepsPerRevolutionX, motor1Pins[0], motor1Pins[1], motor1Pins[2], motor1Pins[3]);
Stepper motorY(stepsPerRevolutionY, motor2Pins[0], motor2Pins[1], motor2Pins[2], motor2Pins[3]);
Stepper motorZ(stepsPerRevolutionZ, motor3Pins[0], motor3Pins[1], motor3Pins[2], motor3Pins[3]);

int stepDelayX = 25;
int stepDelayY = 25;

float ultimo_step1 = 0;
float ultimo_step2 = 0;
float ultimo_step3 = 0;

void setup() {
// Establece la velocidad de los motores
motorX.setSpeed(stepDelayX); // Puedes ajustar esta velocidad según sea necesario motorY.setSpeed(stepDelayY);
motorZ.setSpeed(20);
}

void loop() {

//receivedMessage="G0 F600 X15 Y15 Z10,G1 X25 Y15 E0.94529,G1 X25 Y25 E0.94529,G1 X15 Y25 E0.94529";

Facultad de Ingeniería - Universidad Nacional de Lomas de Zamora | 17

while (Serial.available() > 0 && MensajeRecibido==0) {
receivedMessage = Serial.readStringUntil('\r'); Serial.println("Mensaje Recibido");
Serial.println(receivedMessage);
//miCadena.indexOf(subCadena)
if ( receivedMessage.indexOf(",") != -1 && receivedMessage.indexOf(";") != -1){ MensajeRecibido=1;
}
}

if (MensajeRecibido==1){
const char* charMessage = receivedMessage.c_str(); MatrizMovimientos(charMessage);
for (int fila=0; fila <filas; fila++){ motorZ.step(Movimientos[fila][2]*stepsPerRevolutionZ - ultimo_step3); moverRobotSCARA(Movimientos[fila][0], Movimientos[fila][1]); ultimo_step3 = Movimientos[fila][2]*stepsPerRevolutionZ;
}
Serial.println("Terminado");
MensajeRecibido = 0;
receivedMessage = ""; // Limpiar el mensaje recibido delay(1000);
}
for (int i = 0; i < filas; i++) {
for (int j = 0; j < columnas; j++) { Movimientos[i][j] = 0;
}
}
filas=0;
}

Mientras que el módulo de funciones quedaría de la siguiente forma:

void MatrizMovimientos(char texto[]){
for (int i = 0; i < strlen(texto); i++) {
if (texto[i] == ';') {
filas++;
}
}
char *token = strtok(texto, ",;"); for (int i = 0; i < filas; i++) {
for (int j = 0; j < columnas; j++) { Movimientos[i][j] = atoi(token); // Serial.print("Valor Leido: ");
// Serial.println(Movimientos[i][j]); token = strtok(NULL, ",;");
}

Facultad de Ingeniería - Universidad Nacional de Lomas de Zamora | 18

}
}

void moverRobotSCARA(float x, float y) {
// Función para mover el robot SCARA a una posición específica int cuadrante = 0;
x=abs(x);
y=abs(y);

float d = sqrt(x * x + y * y);
float phi = atan2(y, x);
// Calcular los ángulos de las articulaciones mediante cinemática inversa float theta2 = acos((d * d - L1 * L1 - L2 * L2) / (2 * L1 * L2));
float theta1 = phi - atan2(L2 * sin(theta2), L1 + L2 * cos(theta2));
// Convertir los ángulos a pasos para los motores paso a paso
float avanzar1 = ((theta1 - ultimo_step1) * 360)/(2 * PI);
float avanzar2 = ((theta2 - ultimo_step2) * 360)/(2 * PI);

int steps1 = avanzar1 / avance_motor;
int steps2 = avanzar2 / avance_motor;

MoverBrazo(steps1, steps2);

ultimo_step1 = steps1;
ultimo_step2 = steps2;
}

void MoverBrazo(int pasosX, int pasosY){ int timeX = 0;
int timeY = 0;
int timetotal = 0;
if (pasosX!=0 && pasosY!=0){
float relacion = abs(pasosX)/abs(pasosY); stepDelayX = stepDelayX * pow(relacion,(-1)); timetotal = abs(pasosX) * stepDelayX;
} else if (pasosY==0 && pasosX!=0){ timetotal = abs(pasosX)* stepDelayX;
} else {
timetotal = abs(pasosY)* stepDelayY;
}

for(int i=0;i<=timetotal;i++){
if (i-timeX >= stepDelayX){
if (pasosX>0){
motorX.step(1);
} else if (pasosX<0){
motorX.step(-1);
}

Facultad de Ingeniería - Universidad Nacional de Lomas de Zamora | 19

timeX = i;
}
if (i-timeY >= stepDelayY){ if (pasosY>0){
motorY.step(1);
} else if (pasosY<0){
motorY.step(-1);
}
timeY = i;
}
delay(1);
}
}

### 2.5.3 Código para el ESP32 CAM

#include <WiFi.h>

#include <HTTPClient.h>

const char* ssid = "Repetidor";
const char* password = "53EW9e527c2fAeBb3a2d";
const char* spreadsheetId = "13_MIWFoQno4I7jppms3PyK7UoSv1RYUoeWZiwnOPLt0"; const char* sheetName = "Hoja 1";
const char* apiKey = "0e1c00f2a8ca7bc3949755c1b3a4f3386d19e63f";

void setup() {
Serial.begin(115200);
delay(2000);

WiFi.begin(ssid, password);
while (WiFi.status() != WL_CONNECTED) { delay(1000);
Serial.println("Conectando a WiFi...");
}

Serial.println("Conectado a WiFi");

sendDataToGoogleSheets("Hola mundo");
}

void loop() {
// No se requiere ninguna acción en el bucle principal }

void sendDataToGoogleSheets(const String& data) { HTTPClient http;

// Construir la URL de solicitud

Facultad de Ingeniería - Universidad Nacional de Lomas de Zamora | 20

String url = "https://sheets.googleapis.com/v4/spreadsheets/";
url += spreadsheetId;
url += "/values/";
url += sheetName;
url += ":append?valueInputOption=USER_ENTERED&key="; url += apiKey;

// Configurar la solicitud HTTP
http.begin(url);
http.addHeader("Content-Type", "application/json");

// Construir el cuerpo de la solicitud
String jsonBody = "{\"values\": [[\"";
jsonBody += data;
jsonBody += "\"]]}";

// Enviar la solicitud HTTP POST
int httpResponseCode = http.POST(jsonBody);

if (httpResponseCode > 0) {
Serial.print("Datos enviados a Google Sheets. Código de respuesta: "); Serial.println(httpResponseCode);
} else {
Serial.print("Error en la solicitud. Código de error: "); Serial.println(httpResponseCode);
}

http.end();
}

### 2.5.4 Código para la página web

<!DOCTYPE html>
<html>
<head>
<title>Subir archivo de texto y enviar contenido</title>

<script>
function mostrarContenido() {
var fileInput = document.getElementById('archivo'); var file = fileInput.files[0];
var reader = new FileReader();

reader.onload = function(e) {
var contenido = e.target.result;
sessionStorage.setItem('contenidoArchivo', contenido); enviarContenido(contenido); // Llamar a la función para enviar el contenido };

Facultad de Ingeniería - Universidad Nacional de Lomas de Zamora | 21

reader.readAsText(file);
}

function enviarContenido(contenido) {
var messageElement = document.createElement('p'); // Crear un elemento <p> para mostrar el mensaje
document.body.appendChild(messageElement); // Agregar el elemento al cuerpo de la página

// Enviar contenido del archivo a través de una solicitud POST
var url =
'https://script.google.com/macros/s/AKfycbx4OhybyTxnyrfl0gZBD7UVtPMlXKuliM4_bIY-GXVduRwSF4Ywt0MtSQmRvjf01CrcrQ/exec'; // Reemplaza con la URL de tu hoja de cálculo var formData = new FormData();
formData.append('columna1', contenido);

fetch(url, {
method: 'POST',
body: formData
})
.then(function(response) {
// Manejar la respuesta de la solicitud POST
if (response.ok) {
messageElement.textContent = 'Contenido del archivo enviado exitosamente.'; } else {
messageElement.textContent = 'Error al enviar el contenido del archivo.';
}
})
.catch(function(error) {
messageElement.textContent = 'Error en la solicitud POST: ' + error; });
}

function PedirAvance() {
console.log("Se ha hecho clic en el botón.");
// URL del script de Google Apps Script
var scriptUrl =
'https://script.google.com/macros/s/AKfycbzhyA7-li2_mEbGQmF8bA8-YJE-evMOFxLcz24farC0JJgiM2-fcK084o_NPIV4uaXSEw/exec';

// Realiza la solicitud GET usando la función fetch
fetch(scriptUrl)
.then(function(response) {
return response.text();
})
.then(function(data) {
console.log("Respuesta del servidor: " + data);

Facultad de Ingeniería - Universidad Nacional de Lomas de Zamora | 22

var IP = data.replace(/['"]+/g, ''); console.log("Respuesta del servidor: " + IP); window.location.href = 'http://' + IP;
})
.catch(function(error) {
console.error("Error en la solicitud GET: " + error); });
}
</script>

</head>
<body>
<h1>Subir archivo de texto</h1>
<P>Una vez obtenido el archivo.gcode, cambie la extensión de este a .txt y súbelo</P> <input type="file" id="archivo" accept=".txt">
<br><br>
<button onclick="mostrarContenido()">Subir</button>
<button onclick="PedirAvance()">Ver Avance</button> <br><br>
</body>
</html>

La interfaz obtenida quedaría de la siguiente manera:

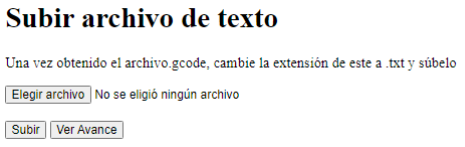
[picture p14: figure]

## 2.6 Explicación del funcionamiento del código

### 2.6.2 Explicación código para el Arduino Uno

Vamos a detenernos específicamente en este punto para poder detallar el método de funcionamiento de la transformación de las posiciones cartesianas obtenidas a la cantidad de pasos que se debe mover cada motor junto con la velocidad a la que deben hacerlo. while (Serial.available() > 0 && MensajeRecibido==0) {
receivedMessage = Serial.readStringUntil('\r');
Serial.println("Mensaje Recibido");
Serial.println(receivedMessage);
//miCadena.indexOf(subCadena)
if ( receivedMessage.indexOf(",") != -1 && receivedMessage.indexOf(";") != -1){

Facultad de Ingeniería - Universidad Nacional de Lomas de Zamora | 23

MensajeRecibido=1;
}
Este fragmento del codigo se utiliza para habilitar la lectura del puerto Serie del arduino en espera del mensaje enviado por el ESP32 con el string que posee las líneas de código a ejecutar por el robot.
void MatrizMovimientos(char texto[]){
for (int i = 0; i < strlen(texto); i++) {
if (texto[i] == ';') {
filas++;
}
}
char *token = strtok(texto, ",;"); for (int i = 0; i < filas; i++) {
for (int j = 0; j < columnas; j++) { Movimientos[i][j] = atoi(token); // Serial.print("Valor Leido: ");
// Serial.println(Movimientos[i][j]); token = strtok(NULL, ",;");
}
}

Seguidamente la primera función a utilizar es la de la generación de la Matriz de movimientos, es decir, se arma una lista con las posiciones finales de cada eje por cada línea de código recibida. Esto me genera una lista con 3 valores en cada elemento, siendo estos valores las posiciones finales de (X, Y, Z) .

void moverRobotSCARA(float x, float y) {
// Función para mover el robot SCARA a una posición específica
int cuadrante = 0;
x=abs(x);
y=abs(y);

float d = sqrt(x * x + y * y);
float phi = atan2(y, x);
// Calcular los ángulos de las articulaciones mediante cinemática inversa float theta2 = acos((d * d - L1 * L1 - L2 * L2) / (2 * L1 * L2));
float theta1 = phi - atan2(L2 * sin(theta2), L1 + L2 * cos(theta2));
// Convertir los ángulos a pasos para los motores paso a paso
float avanzar1 = ((theta1 - ultimo_step1) * 360)/(2 * PI);
float avanzar2 = ((theta2 - ultimo_step2) * 360)/(2 * PI);

int steps1 = avanzar1 / avance_motor;
int steps2 = avanzar2 / avance_motor;

MoverBrazo(steps1, steps2);

ultimo_step1 = steps1;
ultimo_step2 = steps2;

Facultad de Ingeniería - Universidad Nacional de Lomas de Zamora | 24

}

En el caso de la función moverRobotSCARA, es la que transforma las posiciones finales en cantidad de pasos para cada motor, solamente para el caso de los motores 1 y 2 (por eso posee 2 valores de entradas), representantes de los ejes X e Y, ya que, como se definieron como ejes de tipo rotativos, es necesaria una transformación de coordenadas cartesianas a unas polares para su uso.
Debido a la configuración de ejes, se decidió utilizar el método geométrico para el cálculo de ángulos a girar en cada motor a fin de resultar más simple su cálculo. El desarrollo de este metodo lo podemos observar en las primeras lineas de la funcion; pasandolas a lenguaje matematico quedarian:

d = x

2
+ y

2

Calcula la distancia desde el origen al punto final donde se encuentra el extrusor

pℎi = arc tangente (y, x)

Para calcular el ángulo al cual se encuentra el punto final con respecto al eje horizontal

tℎeta2 = arc coseno((d * d − L1 * L1 − L2 * L2) / (2 * L1 * L2))

L1 y L2 representan las longitudes de los brazos 1 y 2 respectivamente.
Esta fórmula se utiliza para calcular el ángulo que hay entre el brazo 2 y la continuación de
la línea central del brazo 1.

tℎeta1 = pℎi − arc tangente(L2 * seno(tℎeta2), L1 + L2 * coseno(tℎeta2))

Finalmente se calcula el ángulo del brazo 1 con respecto del eje horizontal.

Con la secuencia de puntos finales (15,15); (25,15); (25,25); (15,25) los ángulos de theta1 y theta2 deberían quedar de la siguiente manera:

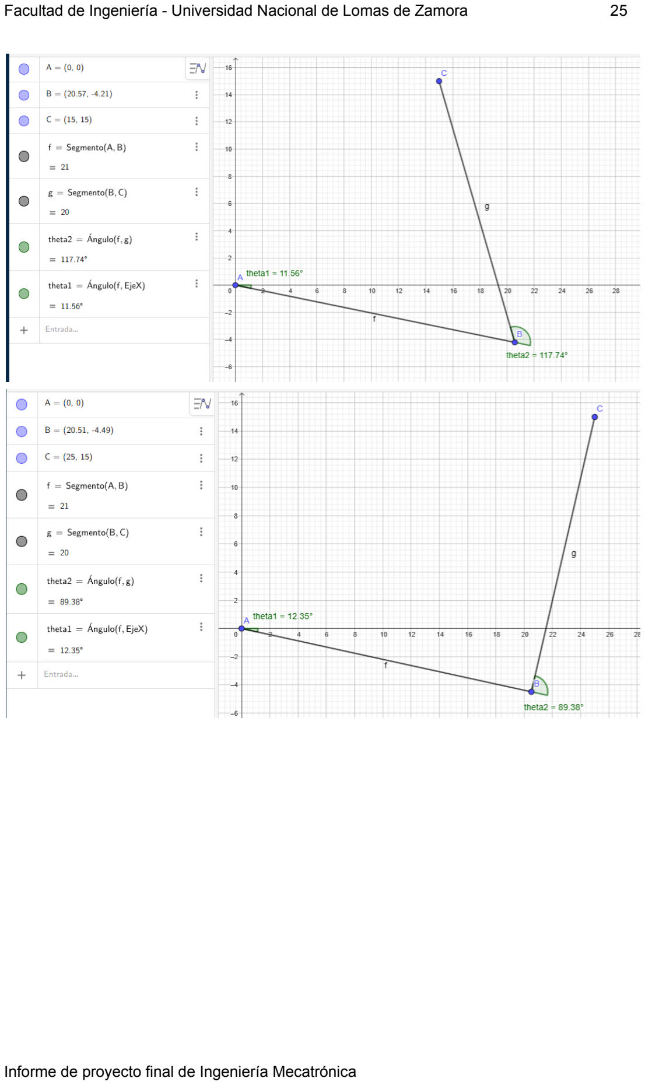
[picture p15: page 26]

Facultad de Ingeniería - Universidad Nacional de Lomas de Zamora | 25

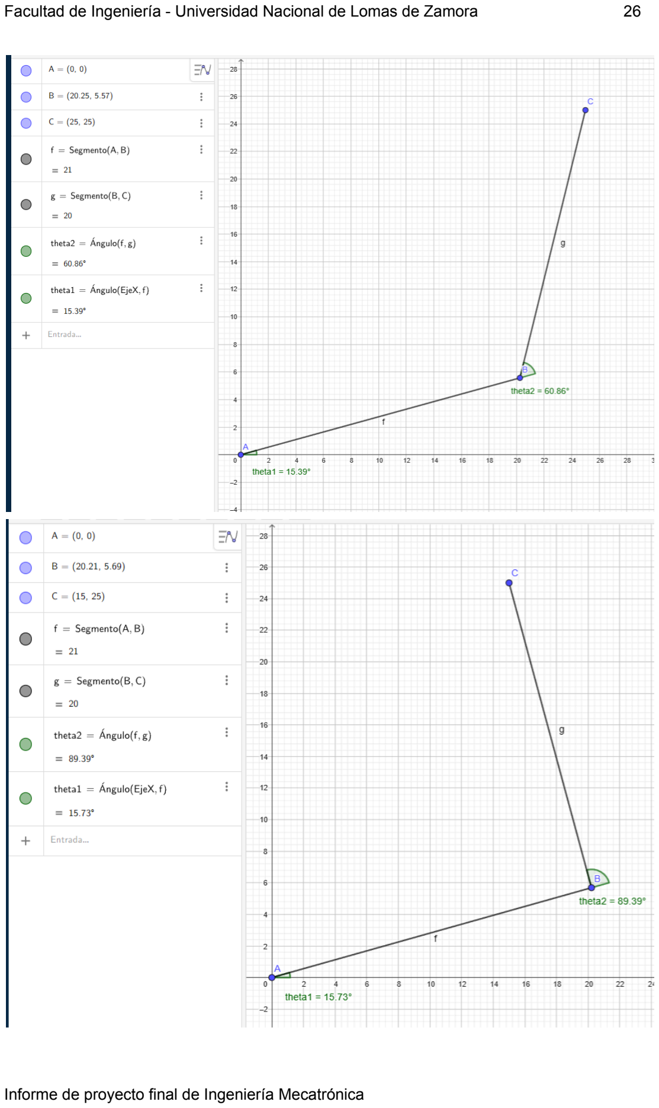
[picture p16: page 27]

Facultad de Ingeniería - Universidad Nacional de Lomas de Zamora | 26

Facultad de Ingeniería - Universidad Nacional de Lomas de Zamora | 27

float avanzar1 = ((theta1 - ultimo_step1) * 360)/(2 * PI);
float avanzar2 = ((theta2 - ultimo_step2) * 360)/(2 * PI);

int steps1 = avanzar1 / avance_motor;
int steps2 = avanzar2 / avance_motor;

A continuación se calcula los ángulos que deben avanzar (o retroceder), cada motor, esto se calcula convirtiendo los ángulos calculados a grados geométricos, ya que inicialmente se encuentran en valores no representativos, es decir, valores no utilizables como grados geométricos.
También se le restara el angulo en el que el motor se encuentra actualmente, reflejado en las variables ultimo_step1 y ultimo_step2, las cuales, luego de cada movimiento se van a ir actualizando. Por ejemplo, si el motor X tiene que posicionarse en 15,73° y actualmente se encuentra en los 15,39°, solamente debería girar 0,34°, que es el valor que se guarda en la variable avanzar1 (la variable avanzar2 es homóloga a avanzar1 pero para el motor 2) Finalmente, a esa cantidad de grados a moverse en cada motor, se lo divide por los grados por pasos del motor (en este caso seria 1.8 grados por paso, que está almacenado en la variable avance_motor), obteniendo la cantidad de pasos a realizar para avanzar esa cantidad de grados geométricos.

MoverBrazo(steps1, steps2);
Una vez terminada toda la serie de cálculos se manda a llamar la funcion MoverBrazo, que es la encargada de coordinar los movimientos de los motores 1 y 2 para que lleguen a su destino al mismo tiempo, generando una línea recta como trayectoria.

void MoverBrazo(int pasosX, int pasosY){
int timeX = 0;
int timeY = 0;
int timetotal = 0;
if (pasosX!=0 && pasosY!=0){
float relacion = abs(pasosX)/abs(pasosY); stepDelayX = stepDelayX * pow(relacion,(-1)); timetotal = abs(pasosX) * stepDelayX;
} else if (pasosY==0 && pasosX!=0){ timetotal = abs(pasosX)* stepDelayX;
} else {
timetotal = abs(pasosY)* stepDelayY;
}

for(int i=0;i<=timetotal;i++){
if (i-timeX >= stepDelayX){
if (pasosX>0){
motorX.step(1);
} else if (pasosX<0){
motorX.step(-1);
}
timeX = i;
}

Facultad de Ingeniería - Universidad Nacional de Lomas de Zamora | 28

if (i-timeY >= stepDelayY){
if (pasosY>0){
motorY.step(1);
} else if (pasosY<0){
motorY.step(-1);
}
timeY = i;
}
delay(1);
}
}

Para que manos motores lleguen al punto de destino al mismo tiempo, sin importar la cantidad de pasos que deba dar cada unos, había varias posibilidades, como por ejemplo utilizar la librería milis de arduino, pero en este caso se decidió hacer una función con un funcionamiento similar pero con delay muy cortos.
El funcionamiento de la función MoverRoborSCARA realiza el cálculo de la relación de pasos que debe dar el motor 1 y el 2, una vez obtenido, afecta al delay o velocidad interna del motor con menos pasos por ese factor, y se obtiene que ambos motores tarden lo mismo aunque den diferente cantidad de pasos. Cabe aclarar que ambos motores ya tienen una velocidad mínima para el movimiento, por eso el factor siempre es aditivo.
Una vez calculado el tiempo que ambos motores tardaran en completar sus correspondientes pasos, se crea un bucle for que itere por cada milisegundo del total calculado, y al final se le coloca un delay de 1 milisegundo, esto hacer que cada ciclo del bucle se ejecute cada 1 milisegundo. Esto nos permite ver si, el delay de cada motor, es decir, la cantidad de milisegundos que tardan en dar cada paso, corresponde con el número de ciclo que se está ejecutando, el motor se mueva un paso. Esto afecta a ambos motores al mismo tiempo.
Cuando se tiene que mover un paso cualquiera sea el motor, se agrega un condicional para saber si se tiene que mover en sentido horario o antihorario, también podría decirse, si se tiene que mover un paso o menos un paso.
Como se puede ver es muy similar el funcionamiento de la librería milis de arduino pero con un agregado de mayor control sobre el tiempo de duración total.

## 2.7 Diagramas de conexionado

### 2.7.1 Conexión ARDUINO - ESP32

La conexión entre todos los componentes quedaría de la siguiente manera.

Facultad de Ingeniería - Universidad Nacional de Lomas de Zamora | 29

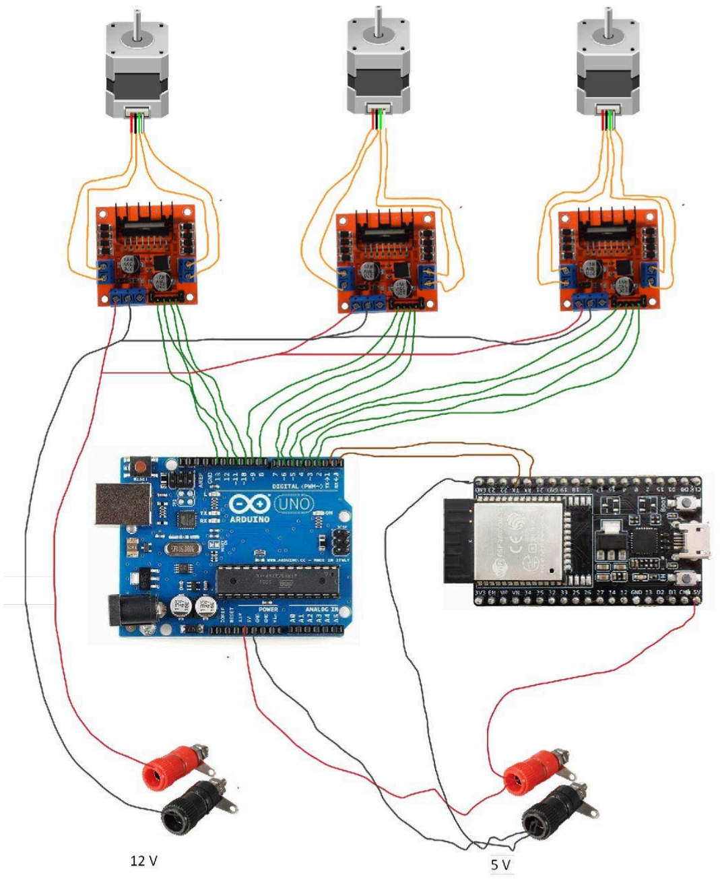
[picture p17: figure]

### 2.7.2 Simulación en Proteus

A fin de mejorar las pruebas y tener una visión más exacta sobre el movimiento de los motores, se decidió simular el circuito y el código del Arduino Uno en el software de simulación electrónica Proteus. El conexionado nos quedaría de la siguiente manera:

Facultad de Ingeniería - Universidad Nacional de Lomas de Zamora | 30

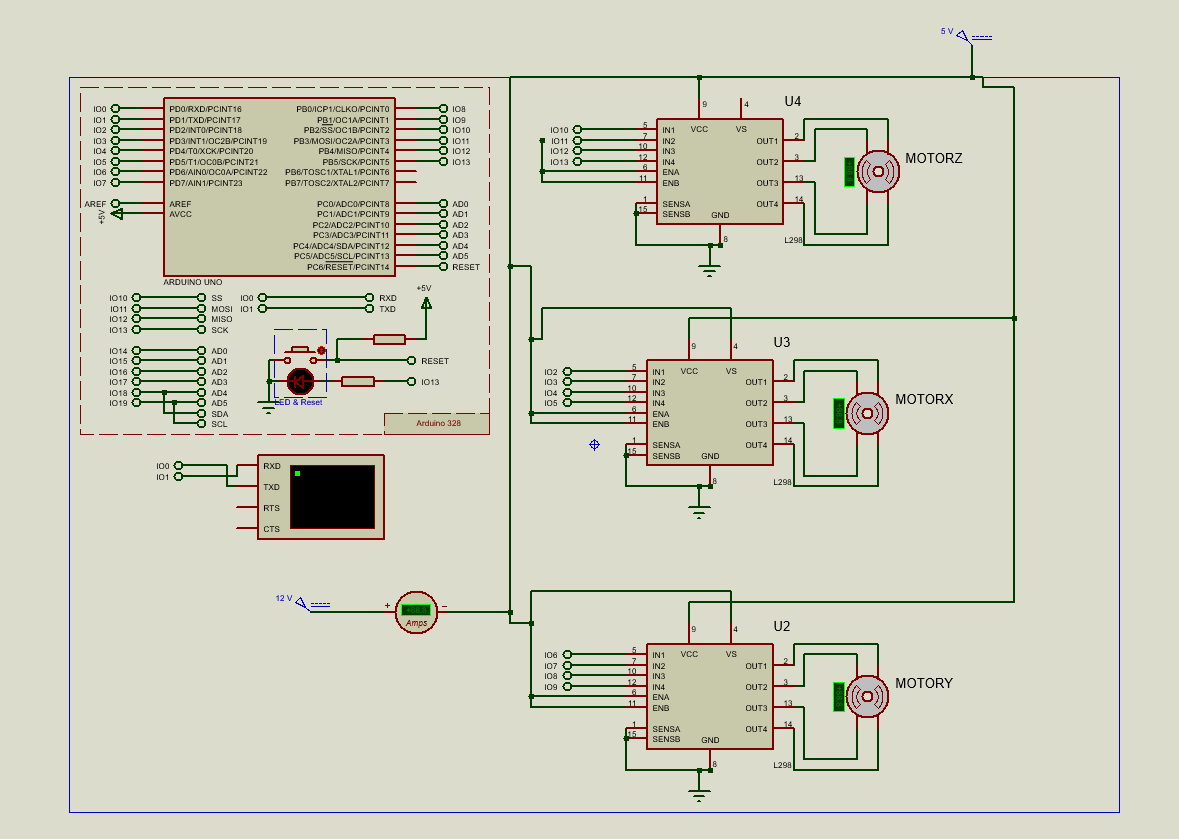
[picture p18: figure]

Facultad de Ingeniería - Universidad Nacional de Lomas de Zamora | 31

# 3. Conclusión

Para finalizar, se logró dimensionar, fabricar y utilizar un un brazo robótico que funciona como impresora 3D. Utilizando 3 placas de desarrollo como lo son Arduino Uno, ESP32 y ESP32 CAM.
El diseño fue hecho con una eje de movimiento prismático para el movimiento vertical (en Z) del brazo, y otros 2 rotativos que se utilizan para el en X e Y, con una distribución tipo SCARA.

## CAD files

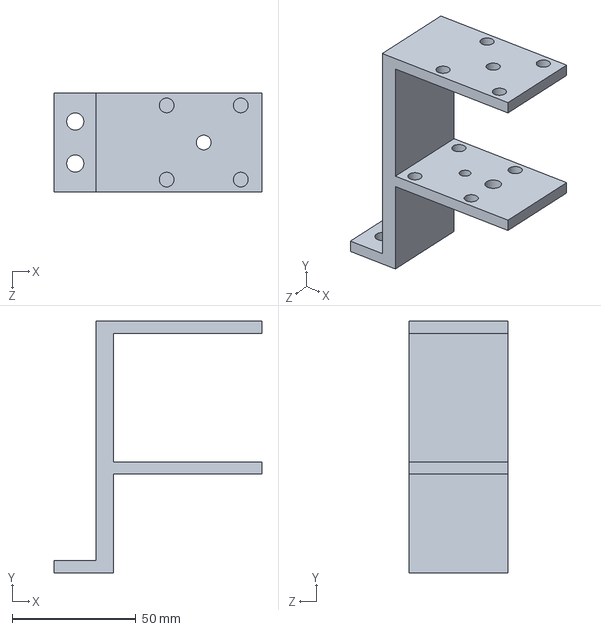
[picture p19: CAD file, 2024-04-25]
Pieces/Base Soporte Motores.SLDPRT
84.0 x 102.0 x 40.0 mm

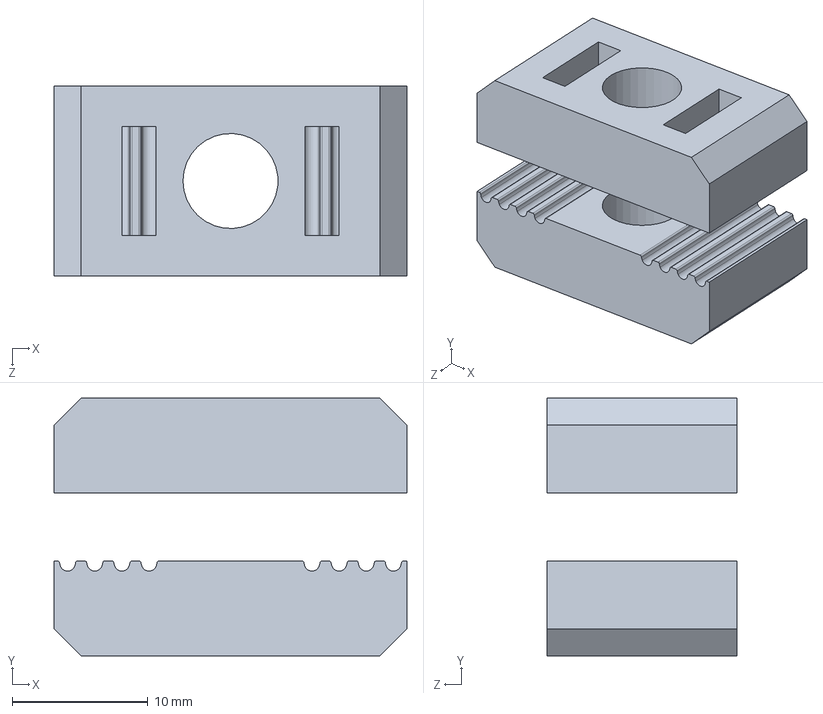
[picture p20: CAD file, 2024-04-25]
Pieces/Tensor correa.SLDPRT
26.0 x 19.0 x 14.0 mm

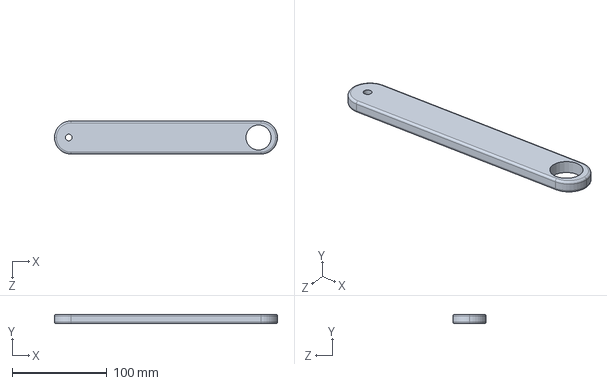
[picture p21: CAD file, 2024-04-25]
Pieces/Brazo L1.SLDPRT
235.0 x 10.0 x 35.0 mm

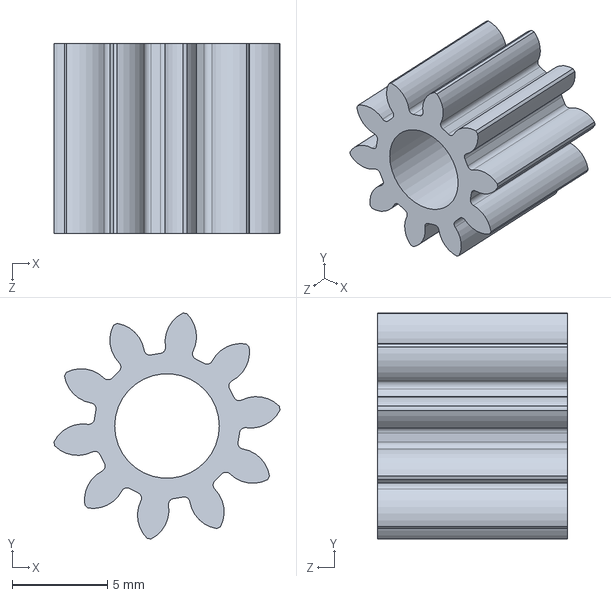
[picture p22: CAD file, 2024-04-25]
Pieces/Engranaje Motor.SLDPRT
11.9 x 11.9 x 10.0 mm

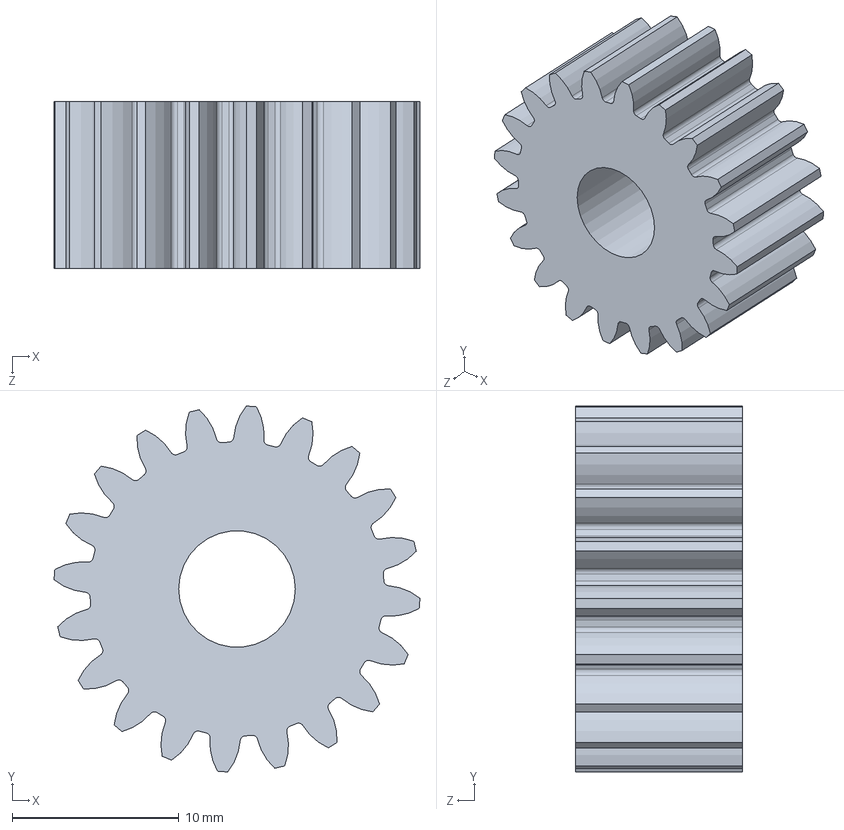
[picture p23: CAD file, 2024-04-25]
Pieces/Engranaje Brazo L1.SLDPRT
22.0 x 22.0 x 10.0 mm

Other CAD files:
Pieces/ensamble.dwg
Pieces/6005.ipt
Pieces/Base Soporte Motores.STL
Pieces/Brazo L1.STL
Pieces/Engranaje Brazo L1.STL
Pieces/Engranaje Motor.STL
Pieces/GUIA INTERIOR.0003.ipt
Pieces/Part1.0002.ipt
Pieces/Part1.ipt
Pieces/TENSOR.ipt
Pieces/Tensor correa.STL
Pieces/base horiz.0004.ipt
Pieces/base plana.0001.ipt
Pieces/base vertical.0002.ipt
Pieces/base.ipt
Pieces/basemedia_2.0002.ipt
Pieces/braazo1.ipt
Pieces/brazo2.ipt
Pieces/chaveta.ipt
Pieces/completo.iam
Pieces/eje.ipt
Pieces/encatre sin fin.0002.ipt
Pieces/engranaje1.iam
Pieces/engranaje2.iam.ipt
Pieces/engranje.ipt
Pieces/ensamble.iam
Pieces/ensamble.ipn
Pieces/escuadra.0001.ipt
Pieces/motor.ipt
Pieces/pared.ipt
Pieces/sin fin.0002.ipt
Pieces/techo.ipt
Pieces/techo2.ipt

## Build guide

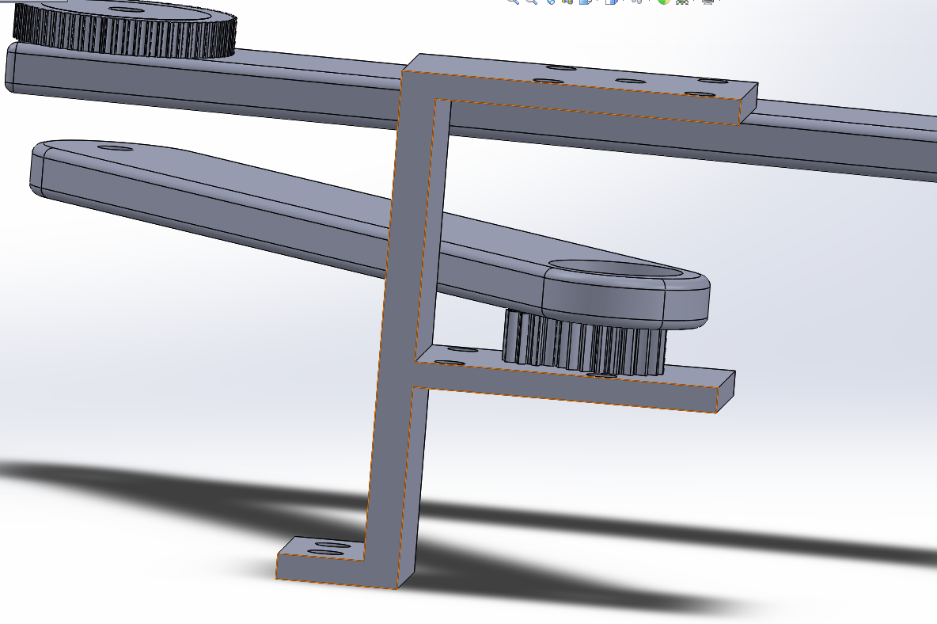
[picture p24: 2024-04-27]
Pieces/Ensamble Brazo2.png

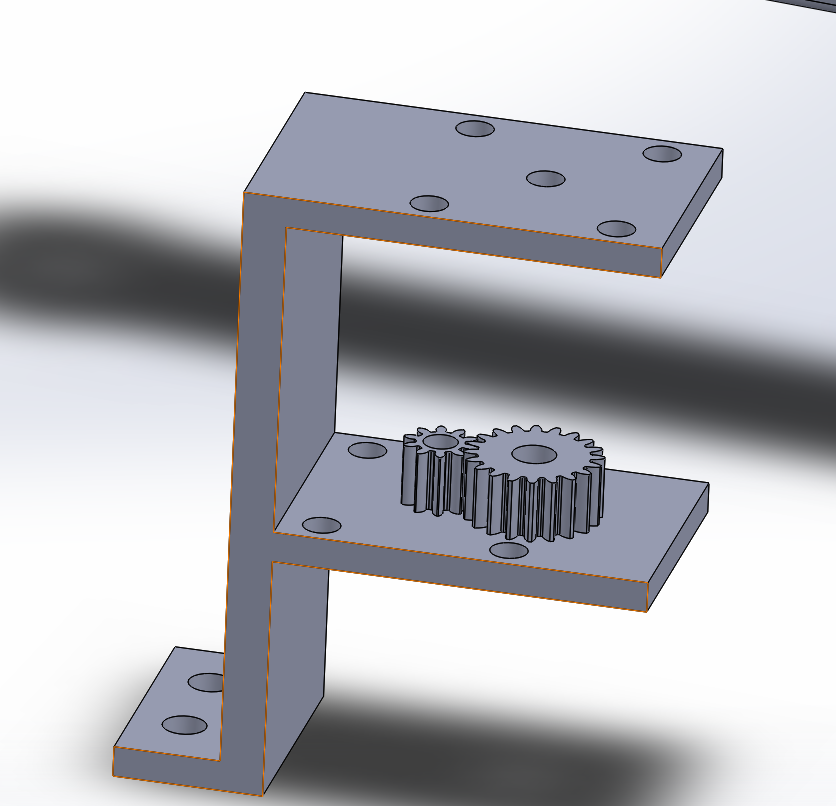
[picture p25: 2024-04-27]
Pieces/Ensamble Brazo1.png

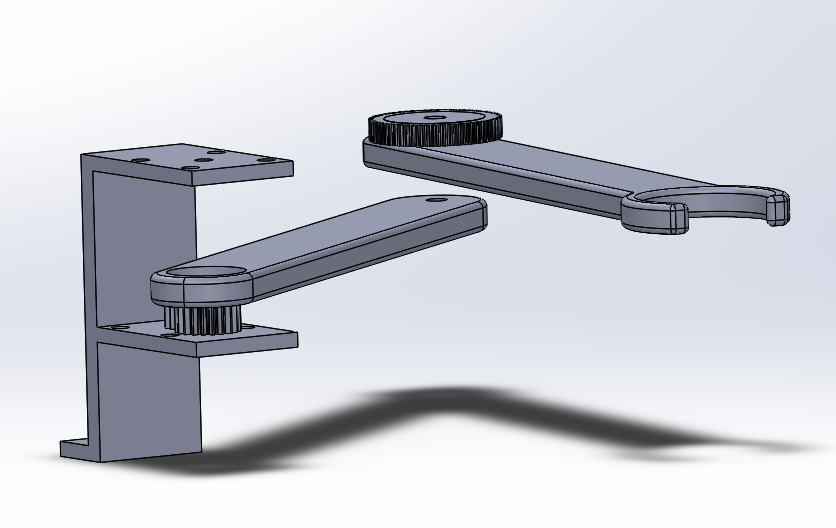
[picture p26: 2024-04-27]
Pieces/Ensamble Brazo3.png

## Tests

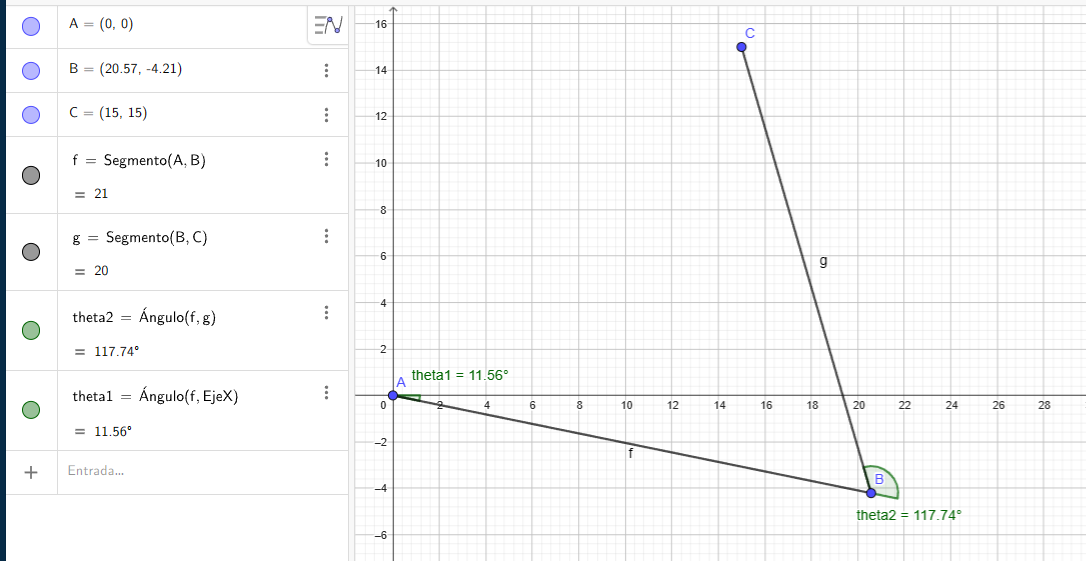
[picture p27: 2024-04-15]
Pruebas/Punto 1.png

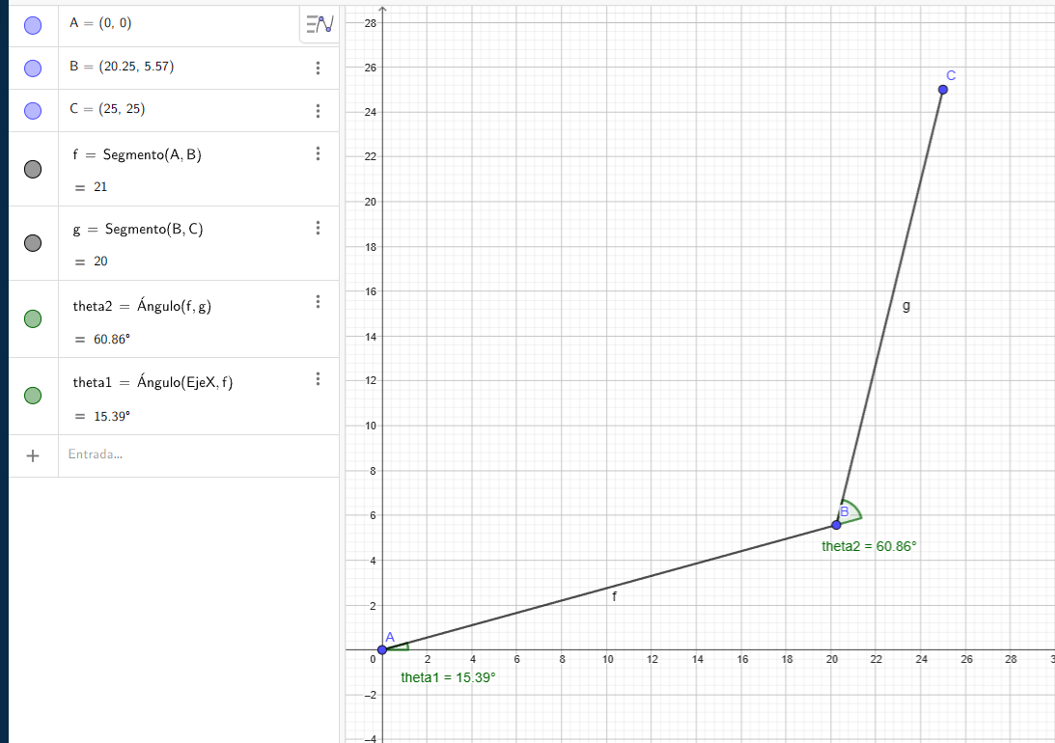
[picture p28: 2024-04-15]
Pruebas/Punto 3.png

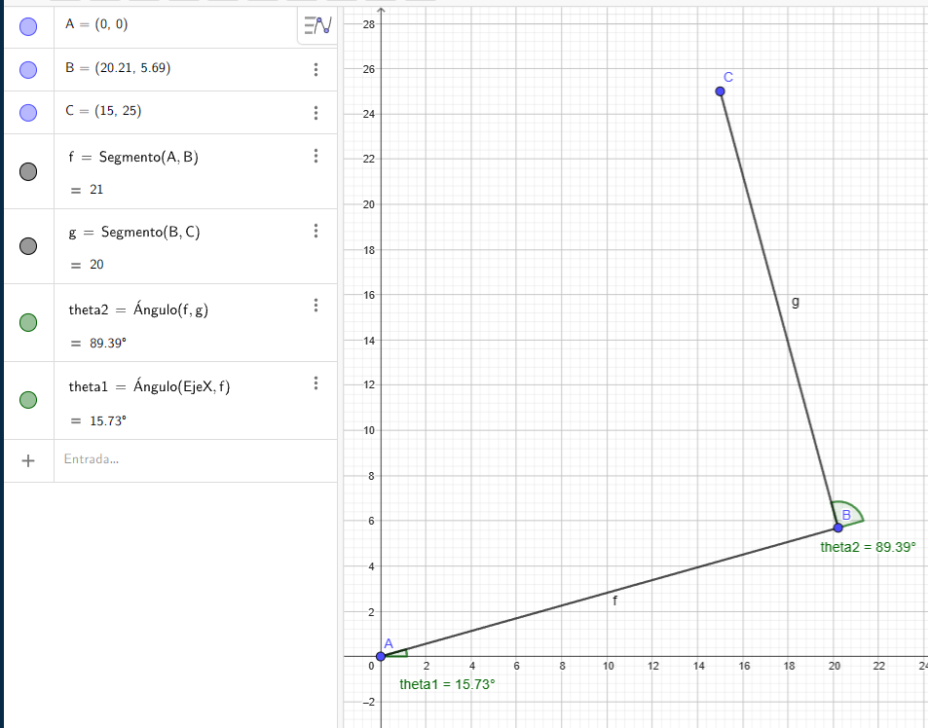
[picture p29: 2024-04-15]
Pruebas/Punto 4.png

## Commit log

2024-04-15 First upload of files
    Program´s files update of the robotic arm 3D printer
2024-04-19 Rename Captura de pantalla 2024-04-19 205139.png to First Step.png
2024-04-19 Rename Captura de pantalla 2024-04-19 205149.png to Second Step.png
2024-04-19 Rename Captura de pantalla 2024-04-19 205201.png to Third Step.png
2024-04-19 Rename Captura de pantalla 2024-04-19 205216.png to Fourth Step.png
2024-04-25 Rename Base Soporte Motores.SLDPRT to Pieces/Base Soporte Motores.SLDPRT
    [Base Soporte Motores.SLDPRT]
2024-04-25 Rename Base Soporte Motores.STL to Pieces/Base Soporte Motores.STL
    [Base Soporte Motores.STL]
2024-04-25 Rename Brazo L1.SLDPRT to Pieces/Brazo L1.SLDPRT
    [Brazo L1.SLDPRT]
2024-04-25 Rename Brazo L1.STL to Pieces/Brazo L1.STL
    [Brazo L1.STL]
2024-04-25 Rename Engranaje Brazo L1.SLDPRT to Pieces/Engranaje Brazo L1.SLDPRT
    [Engranaje Brazo L1.SLDPRT]
2024-04-25 Rename Engranaje Brazo L1.STL to Pieces/Engranaje Brazo L1.STL
    [Engranaje Brazo L1.STL]
2024-04-25 Rename Engranaje Motor.SLDPRT to Pieces/Engranaje Motor.SLDPRT
    [Engranaje Motor.SLDPRT]
2024-04-25 Rename Engranaje Motor.STL to Pieces/Engranaje Motor.STL
    [Engranaje Motor.STL]
2024-04-25 Rename Tensor correa.SLDPRT to Pieces/Tensor correa.SLDPRT
    [Tensor correa.SLDPRT]
2024-04-25 Rename Tensor correa.STL to Pieces/Tensor correa.STL
    [Tensor correa.STL]
